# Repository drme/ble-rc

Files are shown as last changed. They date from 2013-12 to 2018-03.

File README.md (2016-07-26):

# Introduction



Radio controlled cars come with some big radio remotes for controlling them. Those remotes are not really convenient to carry especially then the car model is 1:28 or so, remote is 3-4 times bigger than actual car. Also, each car has its remote, so if we have several cars we have to have several remotes.
So let’s build our own remote – use Smartphone for controlling the cars. In addition, we can use 1 Smartphone to control all cars. The car will provide some API for making more interesting controlling – like automated driving.

# Needed steps
* Get the RC car model
* Make RC cars controlling board
* Install new board into the RC car
* Load app into the Smartphone
* Drive

# Quick build instructions
* Checkout solution from the github (url)
* Manufacture PCB (using fritzing file, and oshpark or friztizng service)
* Build Bluetooth control board firmware and flash it.
* Assemble the board.
* Install the board in the car.
* Load app into the iPhone.

#Car analysis

The simple RC car usually contains one brushed motor for rear wheels driving and one bushed motor for its steering. The driving is limited to the full speed backward and full speed forward. The steering is limited as well, the motor can turn wheels to the left or to the right at the maximum angle, and there are no intermediate driving positions besides centre value. Also then the wheels are turned to some side the motor is stalled, as it keeps turning to the desired position but some gears prevent it from going in that direction – thus motor stalls and gets very warm.

car with 2 motors - drive and steering

In other cars, steering is controlled using magnets – each front wheel is connected to the magnet which attracts the centre knob of the steering mechanism then the voltage is applied to the steering magnet, so if we want to make a left turn, we apply voltage to the left magnet, and if we want to make a right turn, we apply voltage to the right magnet.

Opened and old internals

Some cars also has built-in lights, what’s strange that those lights are not controllable, but just light up than you go forward or backwards.

And finally the car contains some control board that accepts commands from the remote control pad and drives motors, lights, and steering magnets. This board consists of a receiver module and a h-bridge for driving motors (usually just a couple of transistors or FETs are used to make a h-bridge instead of a h-bridge chip) and some transistors for controlling steering magnets or lights.

So let’s build our own controlling board with additional features:
* Controllable by a smartphone instead of a remote controller.
* Several cars can be controlled by the same smartphone (not at once).
* Adjustable driving speed.
* Individually controllable lights (if available).
* Adjustable steering (if possible depending on steering mechanism setup).

# Designing solution

For making car controllable by Smartphone, we will remove its control board, build a new one with a Bluetooth capability, install it in the car, and use the app on the smartphone for controlling it. The whole solution should look like this:

design scheme

* Smartphone with an app – for controlling the car.
* Cars control board, for controlling the car and consisting of:
* Bluetooth module – for phone communication and control. The selected cc2541 module contains Bluetooth module and MCU in one SoC package.
* H-bridge - for driving motors.
* Transistors and resistors – for driving LEDs and steering magnets.
* Voltage regulator and capacitors – for providing stable power to the Bluetooth module.
* PCB – for assembling all components into control board.
* Some firmware for Bluetooth module.
* The actual car

# Designing the board

The board was designed using the frizzing tool. It’s a good idea to start from designing schematics first and then lay outing components on the PCB for board manufacturing. The schematics are presented in the next picture.

schematics

The h-bridge, that drives motors, is direly connected to the Bluetooth module. The Bluetooth module, through h-bridge, can control motors rotation direction and if driven by PWM signal can control the rotation speed as well.

The steering magnets are controlled by two BJT NPN transistors, then the current flows through the transistor base, the transistor opens and it connects the magnets one wire to the ground. When this connection is made, the magnet starts working and attracts the steering magnet, thus turning the wheels. The other wire of the magnet has to be connected to the battery positive side.

The lights are controlled in the similar way as the magnets are. The transistor opens then the current flows through its base, and it connects a LED cathode to the ground. Then this connection is made, the current flows from the battery positive side through the resistor and transistor to the ground and it lights up the LED. The Bluetooth module can control LEDs by applying high or low signals on its connected pins.

The voltage regulator provides power to the Bluetooth module. The selected module requires max 3.3V for operation. In some cases, the car is driven by several batteries, whose provide more voltage (like 5V) than Bluetooth module can handle. This voltage regulator regulates voltage down to the 3.3V and allows running Bluetooth module of all kind of batteries.

The designed PCB consists of two layers and contains SMD components, as in some cases it has to be squeezed into some really small cars. The designed PCB can be easily manufactured using its design files in companies such as oshpark.

pcb top
pcb bottom

Then the PCB is available, the components can be soldered onto it, but before soldering, it would be better to flash initial firmware into the Bluetooth module, which later could accept over the air updates.

assembled board

# Firmware

The control board main part is a cc2541 module by Texas Instruments. This module provides 8051 CPU and Bluetooth radio in one package. The firmware has to be developed using IAR tool that is available as trial version, which is capable of building small firmware images or works for a limited time. Also TI BLE-stack is needed.

The main part of firmware is its Bluetooth Smart GATT table that defines device services and characteristics. So this firmware has one service for controlling a car and this service has several characteristics/attributes:
* 0xacc2 - Steering attribute – the value from 0 to 700, there 350 is centre, 0 is a left turn and 700 is a right turn (and values in the between could be used for precise control).
* 0xacc1 - Throttle attribute – the value from 0 to 700, there 350 is keeps motor off, 0 lets it run backward at full speed and 700 lets it run forward at its full speed (the intermediate values could be used for controlling motor speed, make it run a little bit slower or faster).
* 0xa101 - Lights attribute – depending on written values, the Bluetooth module turns on/off the specified lights. (16-bit number for controlling each individual light. 0x0001 – first light on, 0x0002 -  second light on, 0x0004 third light on, 0x0008 – fourth light on, 0x0010 – fifth light on.)
* Battery voltage attribute – allows monitoring cars battery voltage and to determine if the battery is not running low.

Then the service and its attributes are defined, it’s only left to finish firmware – add code for reacting to attribute changes and adjust motors, steering or lights.

<< Debugger connected>>

Then the firmware is ready it’s time to upload it to the Bluetooth module. The easiest way is to load Over the Air firmware in it, which would allow later updating Bluetooth module firmware directly from a smartphone.

For loading over the air firmware:
* The project has to be built as Simple-Car-OAD-ImageA target
* The BIM project from BLE SDK has to be built as well.
* Connect the Bluetooth module to the CC Debugger.
* Launch Flash Programmer.
* Flash BIM image with Erase, Flash, Verify option.
* Flash Car image with Append, Flash, Verify option.
* If flash was successful, it’s time to assemble the board and proceed to the iOS Application.

flashing

building

# iOS Application

iOS application
Finally, for controlling the car we have to load iOS Application to the smartphone. The application provides the search window for finding all cars and connecting to the selected one. Then the car is connected the applications provides the control window where the steering is controlled by accelerometer (the phone can be rotated as accrual cars wheel) and throttle is adjusted by virtual joystick on the screen. As well, the steering and throttle sensitivity can be adjusted in the settings windows

cars list
controlling

What this application does, it takes values from the accelerometer and the throttle joystick and writes those values to the Bluetooth control chip GATT table. Then those values are written, the control board interprets then and drive the car.

The application is available at the app store, or its source can be checked out from github and compiled with xcode tool.

# Assembling the car

Let’s upgrade some simple car. Here we have the nice car for 1:53 scale. This car can go forward, backwards and make turns to the left and the right. The car is controlled with some remote. If you have several of those tiny cars you have to have a separate remote for each of them.

Initial candidates

Requisites:
* Previously created board.
* Smartphone.
* Smartphone application.
* Some car for hacking.
* Soldering iron and some solder.
* Pliers

unpacked stuff and mcu

So let’s install our constructed Bluetooth module inside of this tiny car and get rid of remote controller, and as a bonus, we could use just one phone for controlling all cars. The cars’ sharing with the friends could be just by passing a car and installing an app on the smartphone.

Opened and old internals

So let’s open this, car. First we have to remove batteries. Inside we have the printed circuit board for receiving commands from remote and controlling the car. The car is driven by small brushed motor; the steering is controlled by two electro-magnets. Then we want to make a turn, the controller applies some current on one of the magnets ant magnet attracts the steering magnet to the desired side and it in turn turns the wheels.

disconnecting old controll borad

So the next step is to remove old control board. We have to disconnect motor – cut be cut or de-soldered, it’s recommended to leave them as long as possible (in this case motor wires are blue and white ones). After that, we have to disconnect battery wires – cut the red and black wires (or de-solder) from the board. The black one goes directly from the battery contacts and the red one goes from the power switch.
Finally, we have to disconnect steering magnets. Those magnets are connected with some tiny wires. Each magnet is connected with 2 wires, depending on how those two wires are connected magnet attracts or pushes steering magnet (reverse the battery for push). In this car, the + sides of both of the magnet is connected to the VCC pad on the control board (it’s recommended to leave those two wires connected together, as we will need than to solder to the new board together as well). The other two wires control the left and right side magnets, those has to be disconnected as well.

adding connectors

The next step is adding connectors. The connectors can be added to the motor and power wires. In the example selected connectors does not need soldering, they required just some work with pliers. We have to strip some isolation from the wire and add metallic connector and its plastic housing.

soldering sterring magnets

The steering wires are more problematic, they are so tiny that there is no easy way to add connectors, so they can be soldered directly to the replacement board. The two connected wires from magnets have to be soldered to the power pad (or could be soldered directly to the battery positive side wire on the car). The remaining wires from the magnets has to be soldered to the two pads on the board – top pad is for the left magnet wire, the second pad for the top is for the right magnet wire.

connecting motor and power

Finally, we have to just plug power connector to the power headers on the board and motor wires to the motor connector, place the board inside the card, and reassemble car back (put the cover and screw it).

reasembling car back and ready to go.

Now it’s time to launch the Smartphone app, turn the car on and start racing.

### Troubleshooting
* Car does not start – check if batteries are installed, check if power wires are connected to the swich, check if power connector to the board is not reversed.
* Car goes backwards instead of forward – reverse motor connector.
* Car turns to the left instead of right – check if magnets wires are soldered to correct pads (just reverse them).
* Steering does not work – check if two power wires from the magnets are together soldered to the VCC pad.

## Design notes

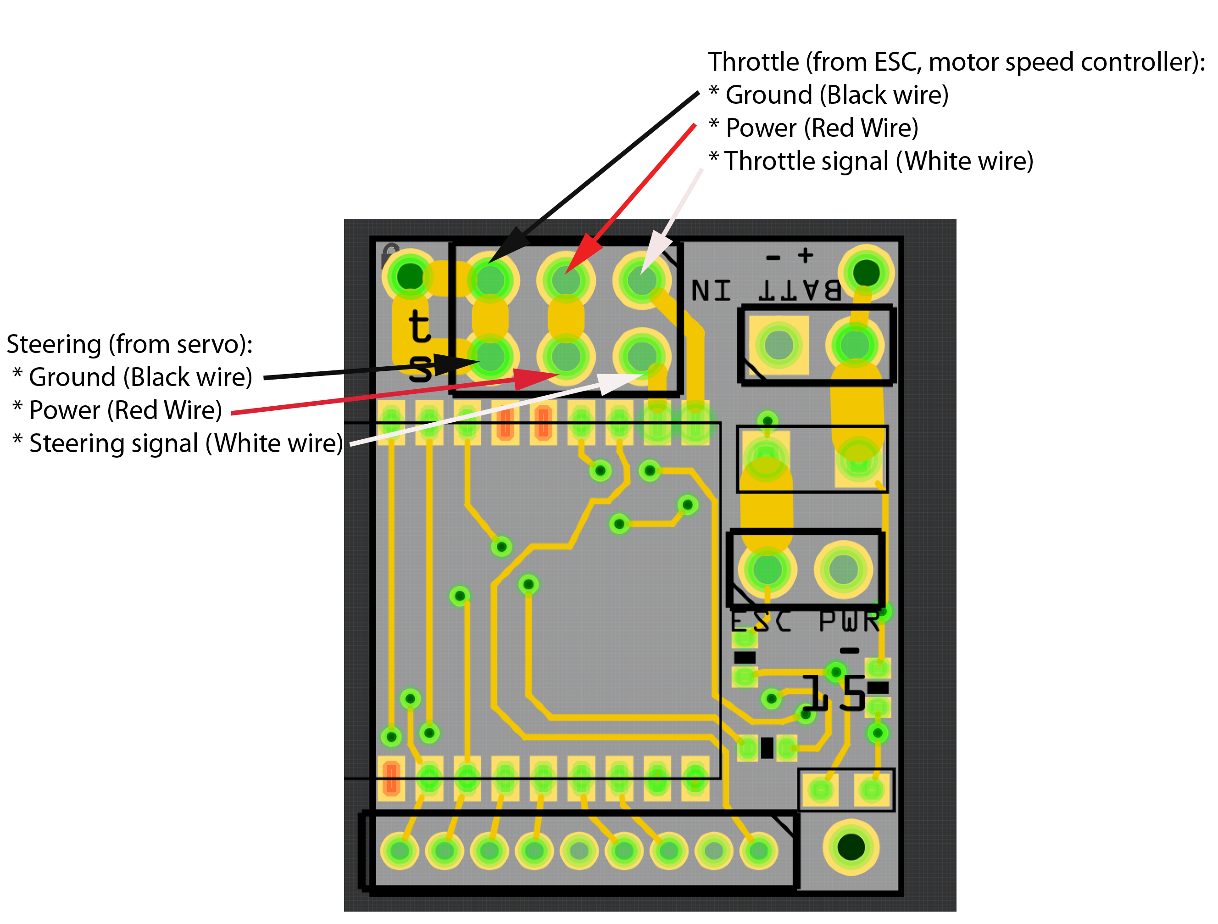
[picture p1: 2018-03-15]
hardware/pcb/ble-rc-receiver-connection.png

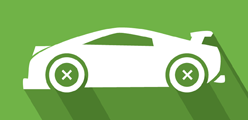
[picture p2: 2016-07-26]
software/windows/SmartRacerWinRT/Assets/sr_558x270.scale-80.png

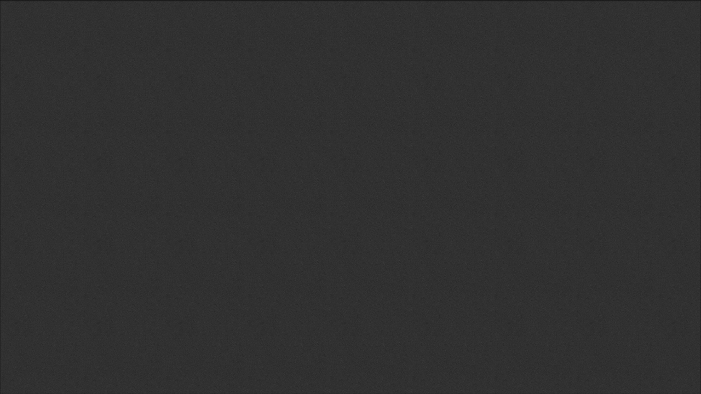
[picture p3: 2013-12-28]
software/windows/SmartRacerWinRT/Assets/background.png

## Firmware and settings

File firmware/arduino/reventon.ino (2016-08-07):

/**
 * Bluetooth control for toy car motors.
 * Accepts commands over bluetooth and drives motors according them.
 * schematics: rc-reventon-arduino.fzz 
 */
#include <IRremote.h>
#include <SoftwareSerial.h>

#define MAX_MILLIS_TO_WAIT 100

const int serialRX = 4;
const int serialTX = 2;

SoftwareSerial mySerial(serialRX, serialTX);
IRsend irsend;

const int None = 0;
const int Left = 1;
const int Right = 2;
const int Back = 4;
const int Forward = 8;
const int Horn = 16;
const int HandBrake = 32;
const int Off = 64;

const int motorFrontWheels1APin = 8;    // H-bridge leg 1 (pin 2, 1A)
const int motorFrontWheels2APin = 12;   // H-bridge leg 2 (pin 7, 2A)
const int enableFrontWheels12Pin = 7;   // H-bridge enable pin
const int enableRearWheels34Pin = 10;   // H-bridge enable pin
const int motorRearWheels4APin = 9;     // H-bridge leg 1 (pin 2, 4A)
const int motorRearWheels3APin = 11;    // H-bridge leg 2 (pin 7, 2A)

const int frontLeftTurnPin = A2;
const int frontRightTurnPin = A0;
const int rearLeftTurnPin = A3;
const int rearRightTurnPin = 13;
const int backPin = A1;

const int hornPin = 5;

void setup()
{
  pinMode(motorFrontWheels1APin, OUTPUT);
  pinMode(motorFrontWheels2APin, OUTPUT);
  pinMode(enableFrontWheels12Pin, OUTPUT);

  pinMode(motorRearWheels4APin, OUTPUT);
  pinMode(motorRearWheels3APin, OUTPUT);
  pinMode(enableRearWheels34Pin, OUTPUT);

  powerOffMotors();

  pinMode(serialRX, INPUT);
  pinMode(serialTX, OUTPUT);

  pinMode(backPin, OUTPUT);
  pinMode(frontLeftTurnPin, OUTPUT);
  pinMode(frontRightTurnPin, OUTPUT);
  pinMode(rearLeftTurnPin, OUTPUT);
  pinMode(rearRightTurnPin, OUTPUT);

  pinMode(hornPin, OUTPUT);
  
  beep(50);
  beep(50);
  beep(50); 

  mySerial.begin(9600);
}
  
void loop()
{
  unsigned long starttime = millis();

  while ((mySerial.available()<1) && ((millis() - starttime) < MAX_MILLIS_TO_WAIT))
  {
  }

  if (mySerial.available() <= 0)
  {
    powerOffMotors();
  }
  else
  {
    int code = mySerial.read();
   
    handleCar(code);
  }
}

void handleCar(int incomingByte)
{
  if ((incomingByte & Left) > 0)
  {
    digitalWrite(enableFrontWheels12Pin, HIGH);      
    digitalWrite(motorFrontWheels1APin, HIGH);
    digitalWrite(motorFrontWheels2APin, LOW);

    digitalWrite(frontLeftTurnPin, HIGH);
    digitalWrite(frontRightTurnPin, LOW);
    digitalWrite(rearLeftTurnPin, HIGH);
    digitalWrite(rearRightTurnPin, LOW);
  }
  else if ((incomingByte & Right) > 0)
  {
    digitalWrite(enableFrontWheels12Pin, HIGH);
    digitalWrite(motorFrontWheels1APin, LOW);
    digitalWrite(motorFrontWheels2APin, HIGH);

    digitalWrite(frontLeftTurnPin, LOW);
    digitalWrite(frontRightTurnPin, HIGH);
    digitalWrite(rearLeftTurnPin, LOW);
    digitalWrite(rearRightTurnPin, HIGH);
  }
  else
  {
    digitalWrite(enableFrontWheels12Pin, LOW);
    digitalWrite(motorFrontWheels1APin, LOW);
    digitalWrite(motorFrontWheels2APin, LOW);

    digitalWrite(frontLeftTurnPin, LOW);
    digitalWrite(frontRightTurnPin, LOW);
    digitalWrite(rearLeftTurnPin, LOW);
    digitalWrite(rearRightTurnPin, LOW);
  }
  
  if ((incomingByte & Back) > 0)
  {
    digitalWrite(enableRearWheels34Pin, HIGH);
    digitalWrite(motorRearWheels4APin, LOW);
    digitalWrite(motorRearWheels3APin, HIGH);
    
    digitalWrite(rearLeftTurnPin, HIGH);
    digitalWrite(rearRightTurnPin, HIGH);
    digitalWrite(backPin, HIGH);
  }
  else if ((incomingByte & Forward) > 0)
  {
    digitalWrite(enableRearWheels34Pin, HIGH);
    digitalWrite(motorRearWheels4APin, HIGH);
    digitalWrite(motorRearWheels3APin, LOW);

    digitalWrite(backPin, LOW);
  }
  else
  {
    digitalWrite(enableRearWheels34Pin, LOW);
    digitalWrite(motorRearWheels4APin, LOW);
    digitalWrite(motorRearWheels3APin, LOW);
  }
  
  if ((incomingByte & Horn) > 0)
  {
    beep(50);
  }
  
  if ((incomingByte & Off) > 0)
  {
    beep(5);
    sendCode(0xa90);
  } 
}

void sendCode(int code)
{
  for (int i = 0; i < 3; i++)
  {
    irsend.sendSony(code, 12);
    delay(50);
  }
} 

void beep(unsigned char delayms)
{
  analogWrite(hornPin, 20);
  delay(delayms);
  analogWrite(hornPin, 0);
  delay(delayms);
}  

void powerOffMotors()
{
  digitalWrite(motorFrontWheels1APin, LOW);
  digitalWrite(motorFrontWheels2APin, LOW);
  digitalWrite(enableFrontWheels12Pin, LOW);
  digitalWrite(enableRearWheels34Pin, LOW);
  digitalWrite(motorRearWheels4APin, LOW);
  digitalWrite(motorRearWheels3APin, LOW);
  
  digitalWrite(frontLeftTurnPin, LOW);
  digitalWrite(frontRightTurnPin, LOW);  
  digitalWrite(rearLeftTurnPin, LOW);
  digitalWrite(rearRightTurnPin, LOW);  
  digitalWrite(backPin, LOW);
}

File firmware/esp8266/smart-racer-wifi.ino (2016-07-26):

#include <ESP8266WiFi.h>
#include <WiFiClient.h>
#include <ESP8266WebServer.h>
#include <ESP8266mDNS.h>
#include <Servo.h>
#include <WiFiUDP.h>
#include <EEPROM.h>
#include <ESP8266HTTPUpdateServer.h>

ESP8266WebServer server(80);
Servo myservo;
Servo esc;
WiFiUDP Udp;
byte packetBuffer[512];
unsigned long lastPacket = millis();
ESP8266HTTPUpdateServer httpUpdater;
int light0Pin = 13;
int light1Pin = 12;
int light2Pin = 16;
int light3Pin = 14;
int light4Pin = 2;
int escPin = 4;
int servoPin = 5;

void handleNotFound()
{
  String message = "File Not Found\n\n";

  message += "URI: ";
  message += server.uri();
  message += "\nMethod: ";
  message += (server.method() == HTTP_GET) ? "GET" : "POST";
  message += "\nArguments: ";
  message += server.args();
  message += "\n";
  
  for (uint8_t i = 0; i < server.args(); i++)
  {
    message += " " + server.argName(i) + ": " + server.arg(i) + "\n";
  }

  server.send(404, "text/plain", message);
};

void handleSettingsValue(uint8_t address)
{
  String value = server.arg("value");

  if (value.length() > 0)
  {
    uint16_t intValue = value.toInt();

    EEPROM.write(address + 0, intValue >> 8);
    EEPROM.write(address + 1, (uint8_t)intValue);

    EEPROM.commit();

    server.send(200, "text/plain", String(intValue));
  }
  else
  {
    uint16_t intValue = (EEPROM.read(address + 0) << 8) | (EEPROM.read(address + 1));
    server.send(200, "text/plain", String(intValue));
  }
};

String getName()
{
  String name = "";

  for (int i = 0; i < 20; i++)
  {
    uint8_t intValue = EEPROM.read(12 + i);

    if ((intValue == 0x00) || (intValue == 0xff))
    {
      break;
    }
    else if (((intValue >= 'a') && (intValue <= 'z')) || ((intValue >= 'A') && (intValue <= 'Z')) || ((intValue >= '0') && (intValue <= '9')) || (intValue == '-') || (intValue == ' ') || (intValue == '_'))
    {
      name += (char)intValue;
    }
  }

  if (name.length() <= 0)
  {
    name = String(ESP.getChipId());
  }

  return name;
};

void handleNameValue()
{
  String value = server.arg("value");

  if (value.length() > 0)
  {
    int i = 0;

    for (i = 0; (i < 19) && (i < value.length()); i++)
    {
      uint8_t v = (uint8_t)value.c_str()[i];

      EEPROM.write(12 + i, v);
    }

    EEPROM.write(12 + i, 0);

    EEPROM.commit();

    server.send(200, "text/plain", value + "->" + getName());
  }
  else
  {
    server.send(200, "text/plain", getName());
  }
};

void handleLight(int pin, bool isOn)
{
  pinMode(pin, OUTPUT);    
  
  if (isOn)
  {
    digitalWrite(pin, LOW);
    server.send(200, "text/plain", "on");
  }
  else
  {
    digitalWrite(pin, HIGH);
    server.send(200, "text/plain", "off");
  }
};

void registerHandlers()
{
  server.on("/settings/steering/min", []() { handleSettingsValue(0); });
  server.on("/settings/steering/max", []() { handleSettingsValue(2); });
  server.on("/settings/steering/center", []() { handleSettingsValue(4); });
  server.on("/settings/throttle/min", []() { handleSettingsValue(6); });
  server.on("/settings/throttle/max", []() { handleSettingsValue(8); });
  server.on("/settings/throttle/center", []() { handleSettingsValue(10); });
  server.on("/settings/name", []() { handleNameValue(); });
  server.on("/", []() { server.send(200, "text/plain", "hello from " + getName()); });
  server.on("/lights/0/on", []() { handleLight(light0Pin, true); });
  server.on("/lights/0/off", []() { handleLight(light0Pin, false); });
  server.on("/lights/1/on", []() { handleLight(light1Pin, true); });
  server.on("/lights/1/off", []() { handleLight(light1Pin, false); });
  server.on("/lights/2/on", []() { handleLight(light2Pin, true); });
  server.on("/lights/2/off", []() { handleLight(light2Pin, false); });
  server.on("/lights/3/on", []() { handleLight(light3Pin, true); });
  server.on("/lights/3/off", []() { handleLight(light3Pin, false); });
  server.on("/lights/4/on", []() { handleLight(light4Pin, true); });
  server.on("/lights/4/off", []() { handleLight(light4Pin, false); });
  server.onNotFound(handleNotFound);
};

void registerFirmwareUpdater()
{
  httpUpdater.setup(&server);
};

void setup(void)
{
  Serial.begin(115200);

  EEPROM.begin(512);

  String apName = "MyRC-" + getName();
  String apPass = "magicpass123";

  Serial.println("Starting ap [" + apName + "] with [" + apPass + "]");

  if (false == WiFi.softAP(apName.c_str(), apPass.c_str()))
  {
    Serial.println("WiFi start failed.. Resetting settings");

    ESP.eraseConfig();
    ESP.reset();
  }
  else
  {
    Serial.println("WiFi start ok");
  }

  server.on("/state", []()
  {
    String servo = server.arg("servo");
    int servoPosition = servo.toInt();

    String escArg = server.arg("esc");
    int escPosition = escArg.toInt();

    setServo(servoPosition);
    setEsc(escPosition);

    server.send(200, "text/plain", "this works as well");
  });

  server.on("/battery", []()
  {
    server.send(200, "text/plain", String(analogRead(A0)));
  });

  registerHandlers();
  registerFirmwareUpdater();

  server.begin();
  Serial.println("HTTP server started");

  Udp.begin(9999);

  handleLight(light0Pin, false);
  handleLight(light1Pin, false);
  handleLight(light2Pin, false);
  handleLight(light3Pin, false);
  handleLight(light4Pin, false);

  pinMode(servoPin, INPUT);
  pinMode(escPin, INPUT);
}

void checkConnectionTimeOut()
{
  unsigned long elapsedTime =  millis() - lastPacket;

  if (elapsedTime > 1000)
  {
    setServo(0xffff);
    setEsc(0xffff);
  }  
};

void setServo(int value)
{
  if (value != 0xffff)
  {
    if (false == myservo.attached())
    {
      pinMode(servoPin, OUTPUT);      
      myservo.attach(servoPin);
    }
    
    myservo.writeMicroseconds(value);
  }
  else
  {
    myservo.detach();
    pinMode(servoPin, INPUT);
  }
};

void setEsc(int value)
{
  if (value != 0xffff)
  {
    if (false == esc.attached())
    {
      pinMode(escPin, OUTPUT);
      esc.attach(escPin);
    }
    
    esc.writeMicroseconds(value);
  }
  else
  {
    esc.detach();
    pinMode(escPin, INPUT);
  }
};

void handleUdpCommands()
{
  int noBytes = Udp.parsePacket();
  String received_command = "";

  if (noBytes)
  {
    lastPacket = millis();

    Udp.read(packetBuffer, noBytes);

    int st = (packetBuffer[0] << 8) | packetBuffer[1];
    int th = (packetBuffer[2] << 8) | packetBuffer[3];

    Serial.println(st, DEC);
    Serial.println(th, DEC);

    setServo(st);
    setEsc(th);
  }
};

void loop(void)
{
  server.handleClient();

  handleUdpCommands();

  checkConnectionTimeOut();
};

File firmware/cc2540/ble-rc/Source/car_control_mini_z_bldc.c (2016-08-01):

#if defined(FIRMWARE_TYPE_MINIZBLDC)

#include "car_control.h"
#include "OSAL.h"
#include "bcomdef.h"
#include "OnBoard.h"
#include "hci.h"
#include "OSAL_PwrMgr.h"
#include "gatt.h"
#include "gapgattserver.h"
#include "blercprofile.h"
#include "hal_adc.h"

#define PWM_PERIODIC_EVT_PERIOD  20
#define SERVO_UPDATE_EVT_PERIOD  1

#define THROTTLE_CHANNEL_L		T1CC3L
#define THROTTLE_CHANNEL_H		T1CC3H

DECLARE_BATTERY_CONNECT(P0DIR |= (1 << 5), P0SEL &= ~(1 << 5), P0_5, 1);
DECLARE_LIGHTS(P2DIR |= (1 << 2) | (1 << 1); P1DIR |= (1 << 3) | (1 << 5) | (1 << 4), P2SEL &= ~((1 << 2) | (1 << 1)); P1SEL &= ~((1 << 3) | (1 << 5) | (1 << 4)), P2_2, P2_1, P1_3, P1_5, P1_4, true);
uint8* defaultName = "Mini-Z BLDC\0\0\0\0\0\0\0\0\0\0\0\0\0\0\0\0\0\0\0\0\0\0\0\0\0\0\0\0\0\0\0\0\0\0\0\0\0";
uint8 deviceType = 0x01;
bool keepRunninOnNoCommands = false;

static uint16 mainTaskId           = 0;
static uint16 desiredServoPosition = 1020;
static bool   servoAdjusting       = false;

void CarSetDefaultValues()
{
	settings.pulseWidth			= 20;

	settings.throttleMin		= 218;
	settings.throttleMax		= 482;
	settings.throttleCenter	= 351;

	settings.steeringMin		= 666;
	settings.steeringMax		= 1446;
	settings.steeringCenter	= 1073;

	settings.batteryCalibration	= 0xa000;

	settings.mainLightNo		= 0;
	settings.backLightNo		= 1;
	settings.reverseLightNo	= 2;
	settings.leftLightNo		= 3;
	settings.rightLightNo		= 4;
	
	
	settings.batteryMaxVoltage	= 5000;
	settings.batteryMinVoltage	= 4000;
	settings.currentLimit				= 5000;
	settings.batteryCapacity		= 750;
	
	settings.deviceCapabilities	= HasLights;
};

static void CarReset()
{
	control.throttle        = settings.throttleCenter;
	control.steering        = settings.steeringCenter;
	control.lights          = 0;
	stats.batteryVoltage    = 0;
	stats.batteryCurrent    = 0;
	stats.batteryUsed       = 0;
	stats.engineTemperature = 0;
	stats.mcuTemperature    = 0;
};

static void InitPWMTimers()
{
	uint8 pwmPins = 0x80 | 0x40; // P0.6 and P0.7 as PWM

	P0DIR |= pwmPins;	// Data direction OUT for the PWM pins
	P0SEL |= pwmPins;	// Choose peripheral mode for PWM pins

	PERCFG |= 0x40; //0x03;             //  Move T1 to alternate2 location   ----Move USART1&2 to alternate2 location so that T1 is visible
	
	// Initialize Timer 1
	T1CTL = 0x0C;		// Div = 128, CLR, MODE = Suspended
	T1CCTL0 = 0x4C;		// IM = 1, CMP = Clear output on compare; Mode = Compare

	T1CC0H = 0x02;		// Ticks = 600 (2.4ms)
	T1CC0L = 0x58;		// Ticks = 600 (2.4ms)

	T1CCTL3 = 0x0C;		// IM = 0; CMP = Clear output on compare; Mode = Compare
	T1CCTL4 = 0x0C;		// IM = 0; CMP = Clear output on compare; Mode = Compare

	T1CCTL1 = 0x0C;		// IM = 0; CMP = Clear output on compare; Mode = Compare
	T1CCTL2 = 0x0C;		// IM = 0; CMP = Clear output on compare; Mode = Compare

	T1CNTL = 0;			// Reset timer to 0;

	IEN1 |= 0x02;		// Enable T1 cpu interrupt

	// Set up the timer registers
	// Ticks = 375 (1,5ms initial duty cycle)
	CarReset();

	T1CTL ^= 0x02;		// timer is off initially
	
	CarTick();
};

static void SetP20PWM(int dutyCycle)
{
	if (dutyCycle <= 0)
	{
		T4CTL = 0x00; // stop timer
		
		P2DIR |= (1 << 0);
		P2SEL &= ~(1 << 0);
		P2_0 = 0;
	}
	else
	{
		PERCFG |= (1 << 4);  // Timer 4 on alternative 2 location		
		P2DIR |= (1 << 0);
		P2SEL |= (1 << 0);
		
		T4CC0 = 0xff - dutyCycle;
		T4CCTL0 = 0x1C;
		T4CTL = 0xF0; // start, free running 0-255, tick/128
	}
};

static void SetP16PWM(int dutyCycle)
{
	if (dutyCycle <= 0)
	{
		T3CTL = 0x00; // stop timer
		
		P1DIR |= (1 << 6);
		P1SEL &= ~(1 << 6);
		P1_6 = 0;
	}
	else
	{
		PERCFG |= (1 << 5);  // Timer 3 on alternative 2 location		
		P1DIR |= (1 << 6);
		P1SEL |= (1 << 6);

		T3CC0 = 0xff - dutyCycle;
		T3CCTL0 = 0x1C;
		T3CTL = 0xF0; // start, free running 0-255, tick/128
	}
};

void CarInit(uint8 taskId)
{
	mainTaskId = taskId;

 	P0SEL = 0x00;
	P0DIR = 0x00;
	P0 = 0x00;

 	P1SEL = 0x00;
	P1DIR = 0x00;
	P1 = 0x00;

 	P2SEL = 0x00;
	P2DIR = 0x00;
	P2 = 0x00;
	
	SetP20PWM(0);
	SetP16PWM(0);
	
	InitPWMTimers();
	CarReset();

	desiredServoPosition = settings.steeringCenter;
};

void CarSetSteering(uint16 value)
{
//	control.steering = value;
	
	desiredServoPosition = value;
};

void SetStatusConnected()
{
};

void CarSetThrottle(uint16 value)
{
	control.throttle = value;
};

void CarConnected()
{
	CarReset();
//	CarTick();
	SetStatusConnected();
	
	CarPPMTick();
};

void CarDisConnected()
{
	CarReset();
	SetStatusConnected();
//	CarTick();
	
	
//		P2DIR |= (1 << 0);
//	P1DIR |= (1 << 6);

//	P2SEL &= ~(1 << 0);	
	
	
	SetP20PWM(0);
	SetP16PWM(0);
};

void CarTick()
{
	
	//if (true == stats.connected)
	{
		osal_start_timerEx(mainTaskId, PERIODIC_EVENT, PWM_PERIODIC_EVT_PERIOD);
	}

	THROTTLE_CHANNEL_L = (uint8)control.throttle;
	THROTTLE_CHANNEL_H = (uint8)(control.throttle >> 8);

	// Make sure timer will count continously
	HCI_EXT_ClkDivOnHaltCmd(HCI_EXT_DISABLE_CLK_DIVIDE_ON_HALT);

	#if defined (POWER_SAVING)
		osal_pwrmgr_device(PWRMGR_ALWAYS_ON);
	#endif

	// Reset timer
	T1CNTL = 0;

	// Start timer in modulo mode.
	T1CTL |= 0x02;
};

void CarUpdateStatus()
{
	HalAdcSetReference(HAL_ADC_REF_125V);
	
	uint16 battery = HalAdcRead(HAL_ADC_CHN_AIN1, HAL_ADC_RESOLUTION_10);

	battery = 1250 * battery * 2 / 1023;
	
	stats.batteryVoltage = battery;
};

////// servoi/////////////////////////////

static int lastServoMotorSpeed = 0;
static long servoError[10] = { 0 };
static long servoAccumulator = 0;

//static uint16 actualServoPosition = 0;






void UpdateError(uint16 currentPosition)
{
  /*
	if (fabs(currentPosition - actualServoPosition) > 10) //2)//3)
	{
		actualServoPosition = currentPosition;
	}
	else
	{
		actualServoPosition = currentPosition;
	}
      */
	// shift error values
//	for (int i = 0; i < 10; i++)
//	{
	//	servoError[i + 1] = servoError[i];
//	}

  for (int i = 9; i > 0; i--)
  {
	servoError[i] = servoError[i - 1];
  }

	// load new error into top array spot
	servoError[0] = (long)desiredServoPosition - (long)currentPosition;//actualServoPosition;
};

int CalculatePID()
{
	float pTerm = 255.0f / 850.0f;
	int iTerm = 0;//25;
	int dTerm = 0;
	uint8 divider = 1; //12; //11; //10;

	// Calculate the PID
	float pid = servoError[0] * pTerm;     // start with proportional gain
	//servoAccumulator += servoError[0];  // accumulator is sum of errors
	//pid += iTerm * servoAccumulator; // add integral gain and error accumulation
	//pid += dTerm * (servoError[0] - servoError[9]); // differential gain comes next
	//pid = pid >> divider; // scale PID down with divider

	if (pid >= 255)
	{
		pid = 255;
	}
	else if (pid <= -255)
	{
		pid = -255;
	}

	return -pid;
};

void SetServoMotorSpeed(int speed)
{
	if (speed > 10)
	{
		//P2_0 = 0;
		SetP20PWM(0);
		//P1_6 = 1;
		SetP16PWM(speed);
	}
	else if (speed < -10)
	{
		//P1_6 = 0;
		SetP16PWM(0);
		//P2_0 = 1;
		SetP20PWM(speed * -1);
	}
	else
	{
		//P1_6 = 0;
		SetP16PWM(0);
		//P2_0 = 0;
		SetP20PWM(0);
	}
};
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

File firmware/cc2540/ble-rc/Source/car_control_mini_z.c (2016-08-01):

#if defined(FIRMWARE_TYPE_MINIZ)

#include "OSAL.h"
#include "bcomdef.h"
#include "OnBoard.h"
#include "hci.h"
#include "OSAL_PwrMgr.h"
#include "gatt.h"
#include "gapgattserver.h"
#include "blercprofile.h"
#include "car_control.h"
#include "hal_adc.h"
#include "math.h"

DECLARE_BATTERY_CONNECT(P1DIR |= (1 << 6), P1SEL &= ~(1 << 6), P1_6, 0);
DECLARE_LIGHTS(;, ;, P2_2, P2_1, P0_2, P0_7, P1_5, false);
uint8* defaultName = "Mini-Z\0\0\0\0\0\0\0\0\0\0\0\0\0\0\0\0\0\0\0\0\0\0\0\0\0\0\0\0\0\0\0\0\0\0\0\0\0\0\0\0\0\0";
uint8 deviceType = 0x00;
bool keepRunninOnNoCommands = false;

static float maxValue = 700.0f;
static uint16 lastThrottleSpeed = 350;
static uint16 desiredServoPosition = 1020;
//static uint16 actualServoPosition = 0;
static int lastServoMotorSpeed = 0;
static long servoError[10] = { 0 };
static long servoAccumulator = 0;
static uint8 mainTaskId = 0;

void CarSetDefaultValues()
{
	settings.throttleMin       = 0;
	settings.throttleMax       = 700;
	settings.throttleCenter    = 350;

	settings.steeringMin       = 666;
	settings.steeringMax       = 1446;
	settings.steeringCenter    = 1073;

	settings.batteryMaxVoltage = 5000;
	settings.batteryMinVoltage = 4000;
	settings.currentLimit      = 5000;
	settings.batteryCapacity   = 750;
	
	settings.deviceCapabilities	= 0;
};

void CarReset()
{
	// no connection no pwm..	
	
	T1CC4L = 0;
	T1CC4H = 0;	
	
	T1CC3L = 0;
	T1CC3H = 0;

	T1CC1L = 0;
	T1CC1H = 0;	
	
	T1CC2L = 0;
	T1CC2H = 0;

	T1CNTL = 0;		
	
	//    P0SEL &= ~((1 << 6) | (1 << 5));        P0_5 = 0;     P0_6 = 0;
};

void CarRCInitPWMTimers()
{
	uint8 pwmPins = 0x78; // P0.5, P0.6, P0.4, and P0.3 as PWM

	P0DIR |= pwmPins;	// Data direction OUT for the PWM pins
	P0SEL |= pwmPins;	// Choose peripheral mode for PWM pins

	PERCFG |= 0x03;     //  Move USART1&2 to alternate2 location so that T1 is visible

	T1CC0L = 0xFF;
	T1CC0H = 0xff;

	T1CCTL0 = (T1CCTL0 & ~0x23) | 0x1C; // Channel 0 in compare mode, Set output on compare-up, clear on 0 (50% duty cycle)	

	T1CC1L = 0x1 * 0;  // PWM duty cycle, Channel 1 (P0_3)
	T1CC1H = 0x0;
	T1CCTL1 = (T1CCTL1 & ~0x23) | 0x1C; // Channel 1 in compare mode, Set output on compare-up, clear on compare-down

	T1CC2L = 0x1 * 0;  // PWM duty cycle, Channel 2 (P0_4)
	T1CC2H = 0x00;
	T1CCTL2 = (T1CCTL2 & ~0x23) | 0x1C;  // Channel 2 in compare mode, Set output on compare-up, clear on compare-down

	T1CC3L = 0x1 * 0;  // PWM duty cycle, Channel 3 (P0_4)
	T1CC3H = 0x00;
	T1CCTL3 = (T1CCTL3 & ~0x23) | 0x1C; // Channel 3 in compare mode, Set output on compare-up, clear on compare-down

	T1CC4L = 0x1 * 0;  // PWM duty cycle, Channel 4 (P0_5)
	T1CC4H = 0x00;
	T1CCTL4 = (T1CCTL4 & ~0x23) | 0x1C;  // Channel 4 in compare mode, Set output on compare-up, clear on compare-down
						
	T1CTL |= 0x06;// 0x0A; // divide with 128 and to do i up-down mode

	T1CNTL = 0;			// Reset timer to 0;

	CarReset();
};

void CarInit(uint8 taskId)
{
	mainTaskId = taskId;
	
	P0SEL	= 0x00;
	P0DIR	= 0x00;
	P0		= 0x00;

 	P1SEL	= 0x00;
	P1DIR	= 0x00;
	P1		= 0x00;

	P2SEL	= 0x00;
	P2DIR	= 0x00;
	P2		= 0x00;
	
	CarRCInitPWMTimers();
	
	//IEN0 |= 0x02; // ADC interupt
	
	desiredServoPosition = settings.steeringCenter;
};

void CarSetSteering(uint16 value)
{
	desiredServoPosition = value;
};

void CarSetThrottle(uint16 value)
{
	if (value == lastThrottleSpeed)
	{
		return;
	}

	lastThrottleSpeed = value;
	
	if (value > 400)
	{
		if (value > 695)
		{
			value = 695;
		}
	
		float maxDiff = maxValue - 400.0f;
		float diff = maxValue - value;
	
		float vv = ((float)0xfffe * diff / maxDiff);
		
		uint16 v = (uint16)vv;
		
		T1CC1L = 0;
		T1CC1H = 0;  		
		
		T1CC2L = (uint8)v;
		T1CC2H = (uint8)(v >> 8);	
	}
	else if (value < 300)
	{
		if (value < 3)
		{
			value = 3;
		}	
	
		float maxDiff = 300.0f;
		float diff = value;

		float vv = ((float)0xfffe * diff / maxDiff);
		
		uint16 v = (uint16)vv;

		T1CC2L = 0;
		T1CC2H = 0;	

		T1CC1L = (uint8)v;
	    T1CC1H = (uint8)(v >> 8);
	}
	else
	{
		T1CC1L = 0;
		T1CC1H = 0;	
	
		T1CC2L = 0;
		T1CC2H = 0;
	}
	
	T1CNTL = 0;		
};

void CarConnected()
{
	CarReset();
	
	osal_start_timerEx(mainTaskId, PERIODIC_EVENT, 1);

	P2SEL &= ~((1 << 2) | (1 << 1));
	P2DIR |= (1 << 2) | (1 << 1);
	
	P2_2 = 1;
};

void CarDisConnected()
{
	CarReset();

	P2_2 = 0;
};

void CarUpdateStatus()
{
	stats.engineTemperature = stats.mcuTemperature;
};

void UpdateError(uint16 currentPosition)
{
  /*
	if (fabs(currentPosition - actualServoPosition) > 10) //2)//3)
	{
		actualServoPosition = currentPosition;
	}
	else
	{
		actualServoPosition = currentPosition;
	}
      */
	// shift error values
//	for (int i = 0; i < 10; i++)
//	{
	//	servoError[i + 1] = servoError[i];
//	}

  for (int i = 9; i > 0; i--)
  {
	servoError[i] = servoError[i - 1];
  }

	// load new error into top array spot
	servoError[0] = (long)desiredServoPosition - (long)currentPosition;//actualServoPosition;
};

int CalculatePID()
{
	float pTerm = 255.0f / 850.0f;
	int iTerm = 0;//25;
	int dTerm = 0;
	uint8 divider = 1; //12; //11; //10;

	// Calculate the PID
	float pid = servoError[0] * pTerm;     // start with proportional gain
	//servoAccumulator += servoError[0];  // accumulator is sum of errors
	//pid += iTerm * servoAccumulator; // add integral gain and error accumulation
	//pid += dTerm * (servoError[0] - servoError[9]); // differential gain comes next
	//pid = pid >> divider; // scale PID down with divider

	if (pid >= 255)
	{
		pid = 255;
	}
	else if (pid <= -255)
	{
		pid = -255;
	}

	return -pid;
};

void SetServoMotorSpeed(int speed)
{
  /*

  if (stats.servoPosition > desiredServoPosition)
  {
	speed = 1000;
  }
  else if (stats.servoPosition < desiredServoPosition)
  {
	speed = -1000;
  }
  else
  {
	speed = 0;
  }
*/

  float invertedSpeed = (uint16)(10.0 + 245.0 * (255.0f - (float)fabs(speed)) / 255.0f);
float maxDiff = 255.0f;

 // return;
	if (speed > 20) //50)
	{

	//  latest	speed = (uint16)(200.0 + 40.0 * (255.0f - (float)speed) / 255.0f);
	
//	            speed = (uint16)(100.0 + 140.0 * (255.0f - (float)speed) / 255.0f);

//	  speed = (uint16)(100.0 + 155.0 * (255.0f - (float)speed) / 255.0f);
//	  speed = (uint16)(10.0 + 245.0 * (255.0f - (float)speed) / 255.0f);

	
	  // latest	  speed =
	
	
		//speed = 240; // slow...
	
	
//		int diff = speed;
	
		uint16 v = (uint16)((float)0xfffe * invertedSpeed / maxDiff);
		
		T1CC4L = (uint8)v;
		T1CC4H = (uint8)(v >> 8);	
	
		T1CC3L = 0;
		T1CC3H = 0;		

		//P0_5 = 0; P0_6 = 1;
	}
	else if (speed < -20) //-50)
	{

	// latest  	speed = (uint16)(-200.0 - 40.0 * (-255.0f - (float)speed) / -255.0f);
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

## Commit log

2013-12-28 iOS app, firmware, pcb design
    [buildConfig.cfg, rc-drift-ble-cc2541-small.fzz]
2016-07-25 wifi version
    [rc-drift-ble-cc2541-small.fzz]
2016-07-26 esp8266 version, ble simple version refactor
    [buildConfig.cfg]
2016-07-26 android client
    [proguard.cfg]
2016-07-28 ESC,Servo version firmware for cc2541
    [rc-rec.fzz]
2016-07-29 current sensor support
2016-08-01 MiniZ BLDC version
2016-08-07 old prototype firmware on arduino
    [rc-reventon-arduino.fzz]
